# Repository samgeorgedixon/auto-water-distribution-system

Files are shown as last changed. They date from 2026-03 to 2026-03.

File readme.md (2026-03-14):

# Regulated Irrigation System (RIS)

**Modular, reliable and fine controlled irrigation for home to industrial greenhouses or farms, while adapting to varied temperatures and seasons to conserve water and ensure plant health.**

## Overview

Regulated Irrigation System (RIS) is modular irrigation system designed for everything from a small greenhouse to industrial farm setups. It gives you detailed control over watering routines and is able to adapt its watering output based on temperature and season. It does this while running reliably all year round unattended while conserving water.

From a phone / desktop browser you can schedule routines to water certain sets of plants at different times or intervals for durations based of current environment conditions.

#### Key Features

1. Water Plants (Water Conservation).
2. Any Environment and Scale (Greenhouse / Farm).
3. Reliable (Works for Months / Years).
4. Sustainable (Self Sufficient: Solar / Rain).
5. Relatively Affordable (< ~£100).

#### Modules

This design is made up of multiple modules which allow it to scale to any scenario with them able to sit flat on a table or be easily mounted onto a wall with keyholes.

- Command Module: Central, controlling all other modules based on the routines you have set.
- Switch modules: Add as many as needed where they interface with command to turn on certain ones of its 6 ports to power your water pumps or valves when needed.
- Valves / Pumps: Allow water to be pumped to specific sets of plants for different durations giving you full control.

#### Power

All operates off 1 battery that is charged continuously with a solar panel to ensure it can run for years in remote locations like an allotment or field.

You can then choose to power the pumps and valves by another source like mains or an external battery pack if they require more power in industrial environments.

## Small Greenhouse Scenario

To take advantage of it in this scenario you can have both sides of the greenhouse on different valves because they may get a different amount of sunlight or have different varieties of plant so one side needs more water than the other.

1. Then you can have a pump that is operated with each valve at a time taking water out of a water tank and distributing it but also have another that fills the tank every couple weeks with more water from a water butt.
2. Due to only giving the plants the water they need they will have increased yields, and it will conserve water which is important when using a water butt as when there is little rainfall it will still have leftover water.
3. As well as this due to water duration being done based of temperature, across the year plants will get more water in the summer when they need it more and little to none in the winter when they don’t need it.

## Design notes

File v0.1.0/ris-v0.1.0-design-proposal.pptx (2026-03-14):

## Regulated Irrigation System (RIS)

by Sam Dixon

What is it?

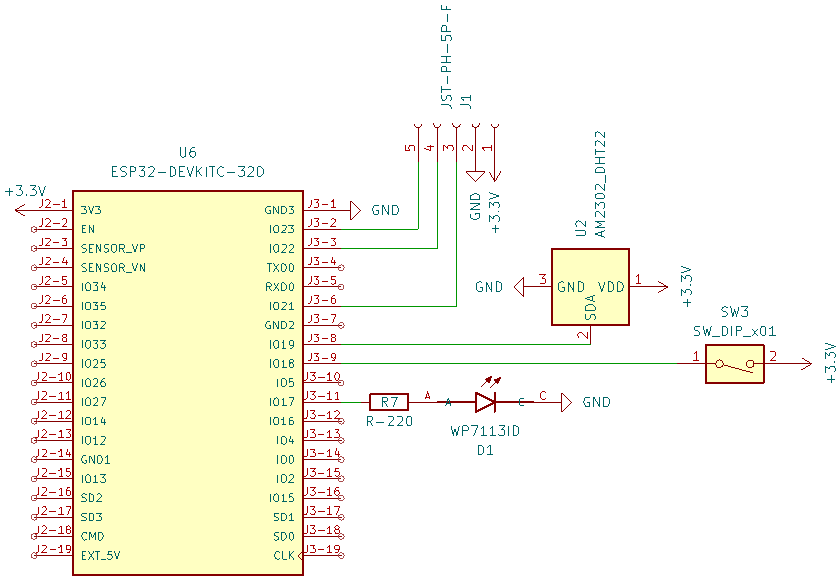
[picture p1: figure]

Command Module
Circuit

Circuit - Electronic Engineering

- This project is all about watering plants in any scenario possible like in a small greenhouse or across an entire farm while being reliable, able to continue working across a whole year through all the seasons.
- The idea for this project came from my Dad’s greenhouse which when we went on holiday was a struggle as no one could water the plants inside it.
- There are many existing products for this issue already, but they are either too expensive for no reason due to being sold to businesses or are too simple and not reliable enough, so I thought I’ll make my own.
- This all led me to my Design Brief I created:
  - Water Plants (Water Conservation).
  - Any Environment and Scale (Greenhouse / Farm).
  - Reliable (Works for Months / Years).
  - Sustainable (Self Sufficient: Solar / Rain).
  - Relatively Affordable (< ~£100).
- A significant portion of this project has been research based as I have been ensuring it can fit my strict design brief with the main consideration being “Any Environment and Scale” because it increases the possible use cases to fit as many users needs as possible.
- I am still currently developing this project and iterating over each area of the design outlined here (titles) over time getting closer to the final design that I will then produce and test as a prototype finally then producing it again as a final product (one-off for now).

Model - Mechanical Engineering

- There will be a circuit in the command and switch modules which I will organise onto 2 custom PCBs that I will get produced by JLCPCB as it is very cheap and scalable for batch production which I may consider if made into a product.
- Command Module which controls the entire system regulating all the valves and pumps at certain times contains: the microcontroller (ESP32), a temperature sensor, Wi-Fi switch, status LED and power management (battery, solar).
- Switch Module has multiple ports to turn on the valves and pumps bridging the gap between them and the command module containing: a shift register (74HC595) that will control relays (SRD-03VDC-SL-C) for each port.
- Each module will communicate using connectors (JST-PH) for power or data.

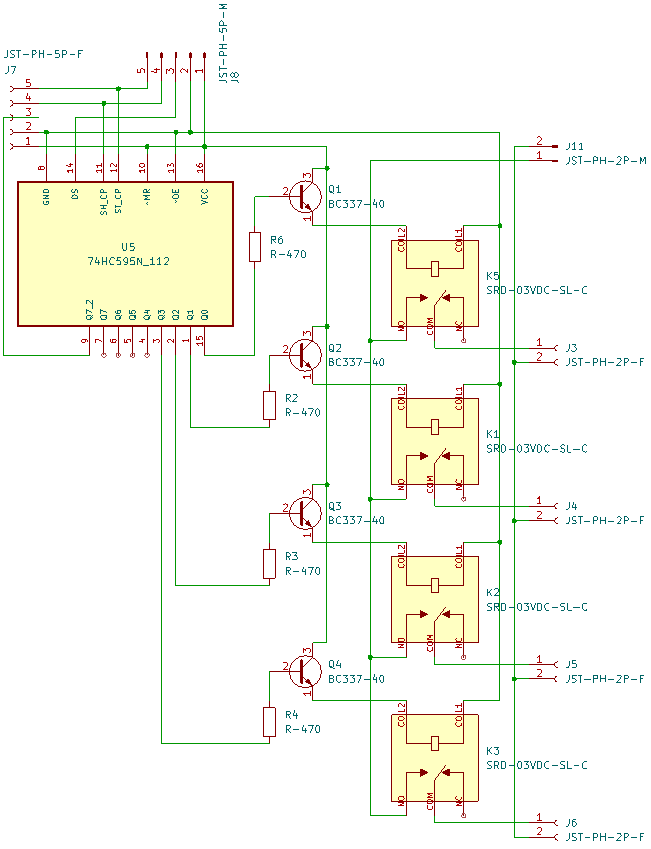
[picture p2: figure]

Switch Module
Circuit

Temp Sensor

Status LED

Wi-Fi Switch

ESP32 (MC)

Command Module

Shift Register

Shift Register

Relay

Relay

…

Valve

Pump

Regulation - Software Engineering

- The microcontroller (ESP32) will control the entire system, regulating all the valves and pumps to ensure they turn on at the required times, with the program (C++ Code) running on it.
- It creates a Wi-Fi Access Point Network with a Web Server as well that users can connect to even in the most remote locations to configure everything using the website interface (on a phone / laptop).
- Routines can then be created that will turn on certain switch ports (Pumps / Valves) at certain times (12:00 every day or month) for a certain duration (60s) to give full control allowing it to be used in any environment.
- This duration can change depending on the temperature sensor, for instance, if its hot (summer) then give plants more water (120s) or if its cold (winter) then give plants little to no water (0s) to allow it to function reliably all year-round while also being sustainable as it is only using the water it needs.
- This ability to use only the water it needs to will allow it to conserve water used in times of shortage and still be able to function through hosepipe bans for instance that have happened recently in the UK.
- All this customisation is given through the simple website that anyone can use to alter the functionality for their personal needs.
- I believe this control for the user is very important as it really sets it apart from the alternatives which really lack any of this leading to the user being unsatisfied with their product which this solves.

…

Switch Module

…

External

- This design is built up of multiple modules to allow it to be scaled up from just a couple plants to hundreds with each being a 3D printed (due to it being more cost effective) case that slide into each other on the sides.
- The Command Module will be the same across all implementations of the product containing the microcontroller (ESP32) for the regulation and a battery with a solar panel on top.
- The Valve Modules contain many slots for electromechanical valves (Solenoid) that can send off water to different areas or types of plants that may want different amount of water.
- The Pumps are external parts of the design that may have module enclosers in the future to protect them while they pump the water to the valves and then plants when needed.
- The Switch Modules control relays for ports to the valves or pumps when needed and can be chained together due to the shift registers inside to allow as many valves and pumps as possible to be added for the required scale.
- An example of an application of this project would be in a greenhouse where the plants on one side need to get more water (due to sunlight) that the other so could be on a different valve port meaning one side has it open for longer than the other allowing full control for the user over their plants or crops (same principle could be applied to a farm).

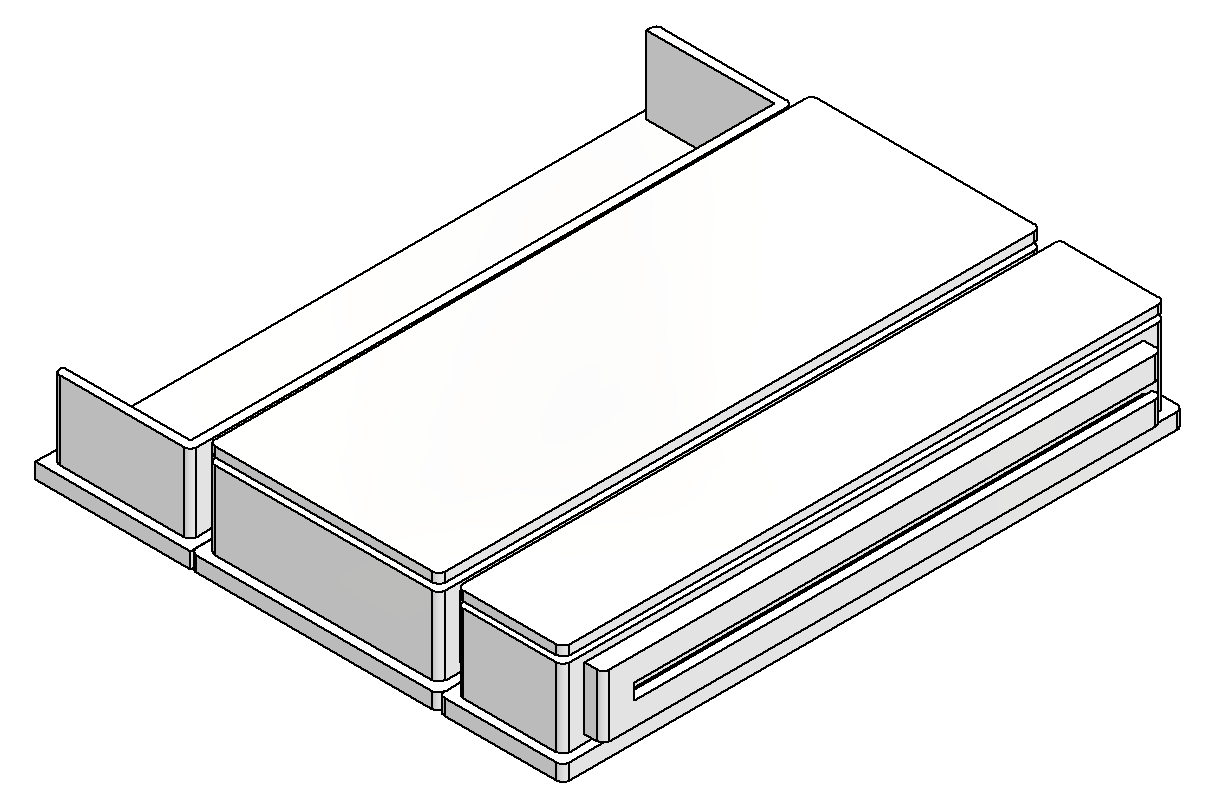
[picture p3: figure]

Valve Module

Command Module

Switch Module

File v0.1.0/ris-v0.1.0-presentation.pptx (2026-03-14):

## Regulated Irrigation System (RIS)

by Sam Dixon

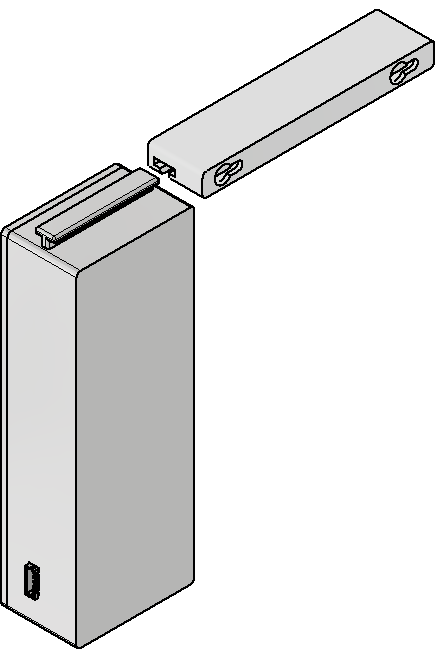
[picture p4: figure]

What is it?

Key Points

- Water Plants (Water Conservation).
- Any Environment and Scale (Greenhouse / Farm).
- Reliable (Works for Months / Years).
- Sustainable (Self Sufficient: Solar / Rain).
- Relatively Affordable (< ~£100).

Wall Mount

- This is an irrigation system all about watering plants in any scenario possible like in a small greenhouse or industrial greenhouse due to giving you full control over its operation while being reliable, able to continue working across a whole year through all the seasons.
- For instance, using the website interface on your phone you can set routines to water certain sets of plants at certain times for a duration based of the current temperature.
- This allows all different types of plants to get the correct amount of water with no wasted.

Power

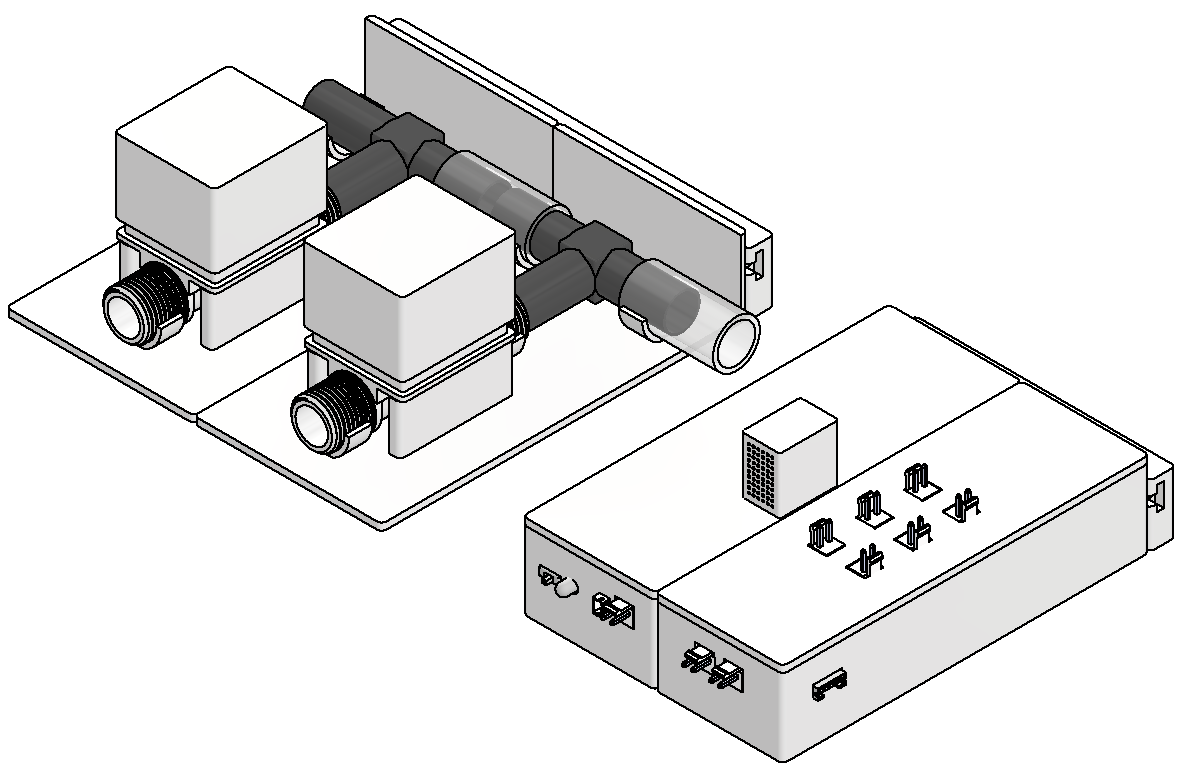
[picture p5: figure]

- It all operates off 1 battery that is charged continuously with a solar panel to ensure it can run for years in remote locations like an allotment or field.
- You can choose to power the pumps and valves by another source like mains or an external battery pack if they require more power in industrial environments.

Modules

- This design is made up of multiple modules which allow it to scale to any scenario with them able to sit flat on a table or be easily mounted onto a wall with keyholes.
- The command module is central, controlling all other modules based on the routines you have set.
- Each valve is chained together on a module to allow water to be pumped to specific sets of plants for different durations giving you control.
- You can add as many switch modules as needed where they interface with command to turn on certain ones of its 6 ports to power the water pumps or valves when needed.

Valve 1

Valve 2

Valve Module

Valve Module

Command
Module

Switch
Module

Ports

## Regulated Irrigation System (RIS)

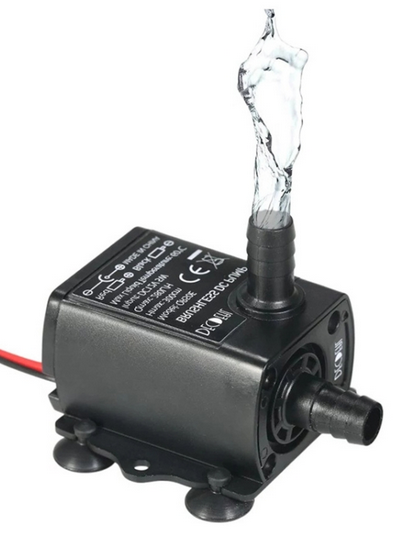
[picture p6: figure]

Pump - 1

by Sam Dixon

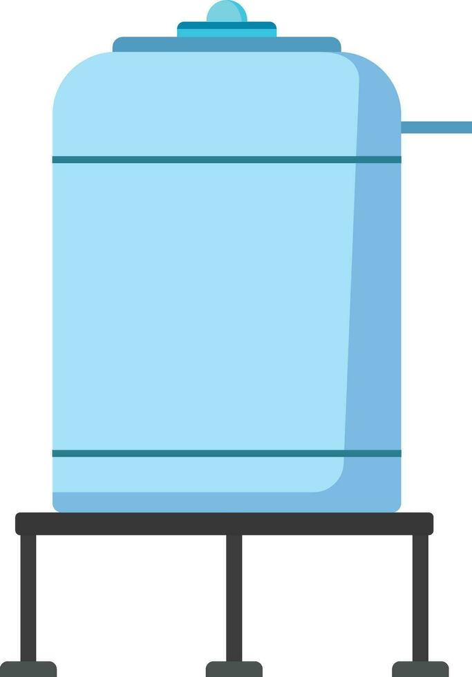
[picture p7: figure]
Water tank flat style vector illustration, Water storage tank, container for storing water, cistern stock vector image 33123783 Vector Art at Vecteezy

Water Tank

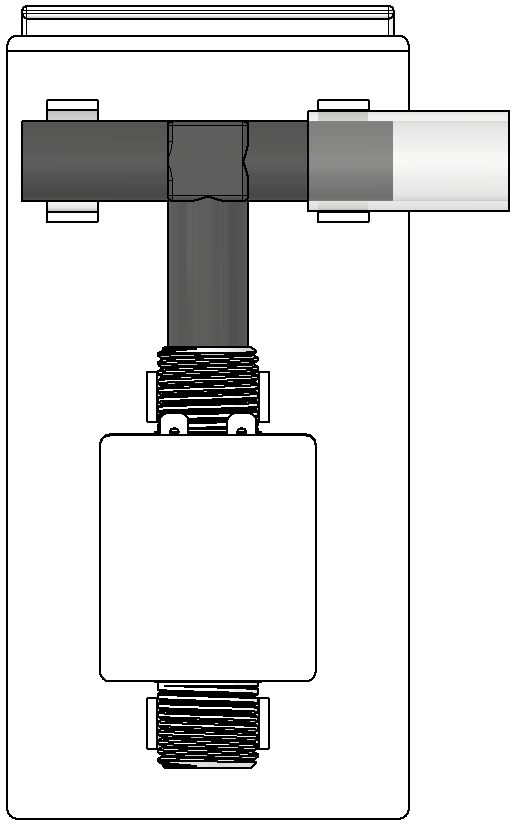
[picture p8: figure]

Valve
Module
1

Valve
Module
2

… Valve Modules

Pump 2

Pump - 2

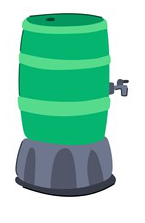
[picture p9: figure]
378 Water Butt Stock Vectors and Vector Art | Shutterstock

Water Butt

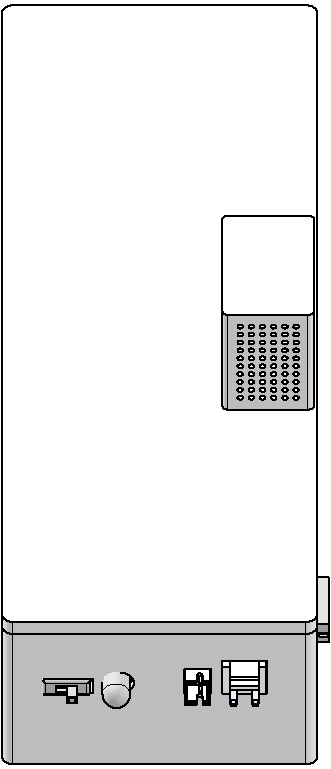
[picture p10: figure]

Command
Module

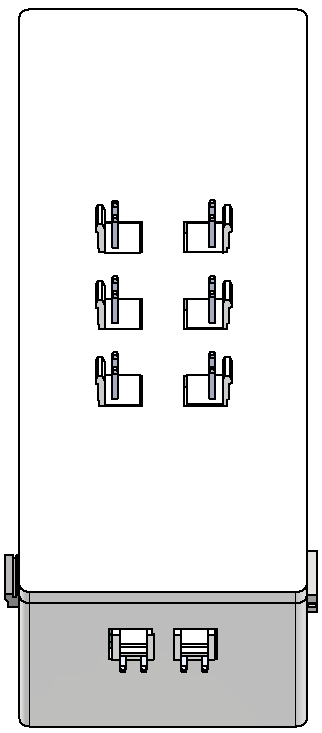
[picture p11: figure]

Switch
Module - 1

Switch
Module - 2

Small Greenhouse Scenario

- To take advantage of it in this scenario you can have both sides of the greenhouse on different valves because they may get a different amount of sunlight or have different varieties of plant so one side needs more water than the other.
- Then you can have a pump that is operated with each valve at a time taking water out of a water tank and distributing it but also have another that fills the tank every couple weeks with more water from a water butt.
- Due to only giving the plants the water they need they will have increased yields, and it will conserve water which is important when using a water butt as when there is little rainfall it will still have leftover water.
- As well as this due to water duration being done based of temperature, across the year plants will get more water in the summer when they need it more and little to none in the winter when they don’t need it.

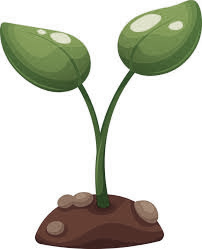
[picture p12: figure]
Sprout of plant, small plant with piece of earth in cartoon style
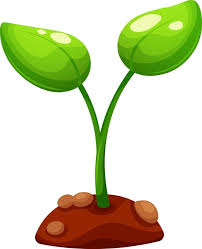
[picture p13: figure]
Sprout of plant, small plant with piece of earth in cartoon style

… Switch Modules

Solar Charging

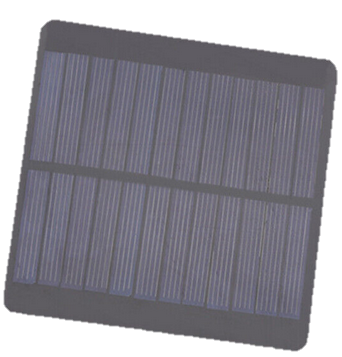
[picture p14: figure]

Solar Panel

Power Chaining …

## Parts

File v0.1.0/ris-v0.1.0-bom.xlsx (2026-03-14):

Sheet: bom
BOM
Component |  |  |  |  | Order
Store | Name | Part Number | Info | Min Quantity | Unit Price | Shipping | PC's | Needed to Buy | Total Price | Shipping Time (Days) | Link
JLCPCB |  |  | PCB's |  |  | £1.12 |  | 1 | £1.12 | 10 - 14 | JLCPCB (https://cart.jlcpcb.com/shopcart/cart?_t=1767553829179&up_spm=Jlcpcb.Loginpage.1003)
- | Command Module | v1.0.0 |  | 1 | £0.86 | £0.00 | 5 | 1 | £0.86 | -
- | Switch Module | v1.0.0 |  | 1 | £0.86 | £0.00 | 5 | 1 | £0.86 | -
LCSC |  |  |  |  | £2.20 | £5.94 |  | 1 | £8.14 | 7 - 15 | LCSC (https://www.lcsc.com/cart)
- | JST-VH Male 2pin | B2P-VH(LF)(SN) |  | 3 | £0.41 | £0.00 | 10 | 1 | £0.41 | - | LCSC (https://www.lcsc.com/product-detail/C160315.html)
- | Switch | SS-12D00-G3 | 2state | 1 | £0.16 | £0.00 | 3 | 1 | £0.16 | - | LCSC (https://www.lcsc.com/product-detail/C22355741.html)
- | JST-PH Male 5pin | B5B-PH-K-S(LF)(SN) |  | 3 | £0.38 | £0.00 | 10 | 1 | £0.38 | - | LCSC (https://www.lcsc.com/product-detail/C157993.html)
- | Mosfet | IRLZ44N(UMW) | 3.3V: 5A-12V | 6 | £3.22 | £0.00 | 15 | 1 | £3.22 | - | LCSC (https://www.lcsc.com/product-detail/C42370423.html)
- | Diode | SB560_AY_10001 | 5A | 6 | £1.34 | £0.00 | 15 | 1 | £1.34 | - | LCSC (https://www.lcsc.com/product-detail/C282379.html)
- | Shift Register | 74HC595N | 8bit | 1 | £0.52 | £0.00 | 5 | 1 | £0.52 | - | LCSC (https://www.lcsc.com/product-detail/C507175.html)
- | JST-PH Male 2pin | B2B-PH-K-S(LF)(SN) |  | 1 | £0.43 | £0.00 | 20 | 1 | £0.43 | - | LCSC (https://www.lcsc.com/product-detail/C131337.html)
- | Header 3pin | PM2.54-1X3P-H85 |  | 1 | £0.11 | £0.00 | 5 | 1 | £0.11 | - | LCSC (https://www.lcsc.com/product-detail/C42431866.html)
 | Header 19pin | PM2.54-1*19 |  | 2 | £0.69 | £0.00 | 5 | 1 | £0.69 | - | LCSC (https://www.lcsc.com/product-detail/C5371990.html?s_z=n_PM2.54-1X19P-H85)
AliExpress |  |  |  |  |  |  |  | 1 | £0.00 | 8 - 12 | AliExpress (https://www.aliexpress.com/p/shoppingcart/index.html?spm=a2g0o.cart.header.1.97d438da5Uqi5N)
- | Temp Sensor | DHT22 |  | 1 | £1.79 | £0.00 | 1 | 1 | £1.79 | - | AliExpress (https://www.aliexpress.com/item/1005010342821748.html?mp=1)
- | Pipe: Flexible PVC |  | 1m: ID-12mm | 1 | £3.09 | £0.00 | 1 | 1 | £3.09 | - | AliExpress (https://www.aliexpress.com/item/1005008851917137.html?mp=1)
- | Pipe Reducer |  | 3.9mm - 12.7mm | 2 | £0.76 | £0.00 | 5 | 1 | £0.76 | - | AliExpress (https://www.aliexpress.com/item/1005005912274158.html?mp=1)
- | Boost Converter | MT3608 | 2A OUT | 2 | £1.89 | £0.00 | 5 | 1 | £1.89 | - | AliExpress (https://www.aliexpress.com/item/1005008953348410.html?mp=1)
- | Wire: JST-VH 2pin |  | 10cm: Double Ended | 2 | £1.27 | £0.00 | 5 | 1 | £1.27 | - | AliExpress (https://www.aliexpress.com/item/1005009025003911.html?mp=1)
- | Wire: JST-PH 2pin |  | 20cm: Single Ended | 1 | £0.90 | £0.00 | 10 | 1 | £0.90 | - | AliExpress (https://www.aliexpress.com/item/1005007270514533.html?mp=1)
- | Wire: JST-PH 5pin |  | 20cm: Single Ended | 2 | £1.82 | £0.00 | 10 | 1 | £1.82 | - | AliExpress (https://www.aliexpress.com/item/1005007270514533.html?mp=1)
- | Pipe Reducer |  | 11.1mm - 15.8mm | 3 | £2.01 | £0.00 | 5 | 1 | £2.01 | - | AliExpress (https://www.aliexpress.com/item/1005005912274158.html?mp=1)
- | Pump | QR50E | 5W: 12V (3m Lift, 280l/h) | 1 | £3.83 | £0.00 | 1 | 1 | £3.83 | - | AliExpress (https://www.aliexpress.com/item/1005007457199939.html?mp=1)
- | Solenoid Valve | FPD-270A | 12V: G1/2" NC | 2 | £3.08 | £0.00 | 1 | 2 | £6.16 | - | AliExpress (https://www.aliexpress.com/item/1005007532380394.html?mp=1)
- | RTC Module | ZS-042 |  | 1 | £1.94 | £0.00 | 1 | 1 | £1.94 | - | AliExpress (https://www.aliexpress.com/item/32985147642.html?mp=1)
- | Battery | 5050100 | 4Ah: 3.7V | 1 | £5.99 | £2.81 | 1 | 1 | £8.80 | 18 | AliExpress (https://www.aliexpress.com/item/32908593252.html?mp=1)
Ebay |  |  |  |  |  |  |  | 1 | £0.00 |  | Ebay (https://cart.ebay.co.uk/)
- | ESP32 | ESP32-DevKitC-v4 |  | 1 | £5.95 | £0.00 | 1 | 1 | £5.95 | 3 - 4 | Ebay (https://www.ebay.co.uk/itm/195759492546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)
- | Battery Charger |  | 1A: 5V IN, 4.2V OUT | 1 | £2.88 | £1.66 | 1 | 1 | £4.54 | 8 - 10 | Ebay (https://www.ebay.co.uk/itm/254771123006?_skw=Li-ion+charge+controller&itmmeta=01KCE8GVJEVT9J6W3MWF6TEBNC)
- | Solar Cell |  | 150mA: 5V | 1 | £2.74 | £0.00 | 1 | 1 | £2.74 | 12 - 16 | Ebay (https://www.ebay.co.uk/itm/335504833393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)
- | Pipe: Flexible PVC |  | 2m: ID-16mm (1/2") | 1 | £3.80 | £0.00 | 1 | 1 | £3.80 | 2 - 3 | Ebay (https://www.ebay.co.uk/itm/333369363332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)
- | T-Piece |  | 1/2" (OD-16mm) | 2 | £3.99 | £0.00 | 2 | 1 | £3.99 | 2 - 3 | Ebay (https://www.ebay.co.uk/itm/133052308194?_skw=T-Piece&itmmeta=01KF5W1XYFVM32WJARDY9XMV77&var=432352315321)
3D Print | Casing (Model) |  | 3D Printed | 1 | £0.00 | £0.00 |  | 1 | £0.00 | 0
Total |  |  |  |  |  |  |  |  | £73.52

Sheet: store-orders
BOM
Component |  |  | Order
Store Basket | Info | Min Quantity | Unit Price | Shipping | Needed to Buy | Total Price | Shipping Time (Days) | Link
JLCPCB | PCB's | 2 | £1.72 | £1.12 | 1 | £2.84 | 10 - 14 | JLCPCB (https://cart.jlcpcb.com/shopcart/cart?_t=1767553829179&up_spm=Jlcpcb.Loginpage.1003)
LCSC | Electronics | 8 | £9.53 | £5.94 | 1 | £15.47 | 7 - 15 | LCSC (https://www.lcsc.com/cart)
AliExpress | Components | 12 | £31.45 | £2.81 | 1 | £34.26 | 8 - 12, 18 | AliExpress (https://www.aliexpress.com/p/shoppingcart/index.html?spm=a2g0o.cart.header.1.97d438da5Uqi5N)
Ebay | Components | 5 | £19.50 | £1.66 | 1 | £21.16 | 9 - 10 | Ebay (https://cart.ebay.co.uk/)
Casing (Model) | 3D Printed | 2 | £0.00 | £0.00 | 1 | £0.00 | 0
Total |  |  |  |  |  | £73.73

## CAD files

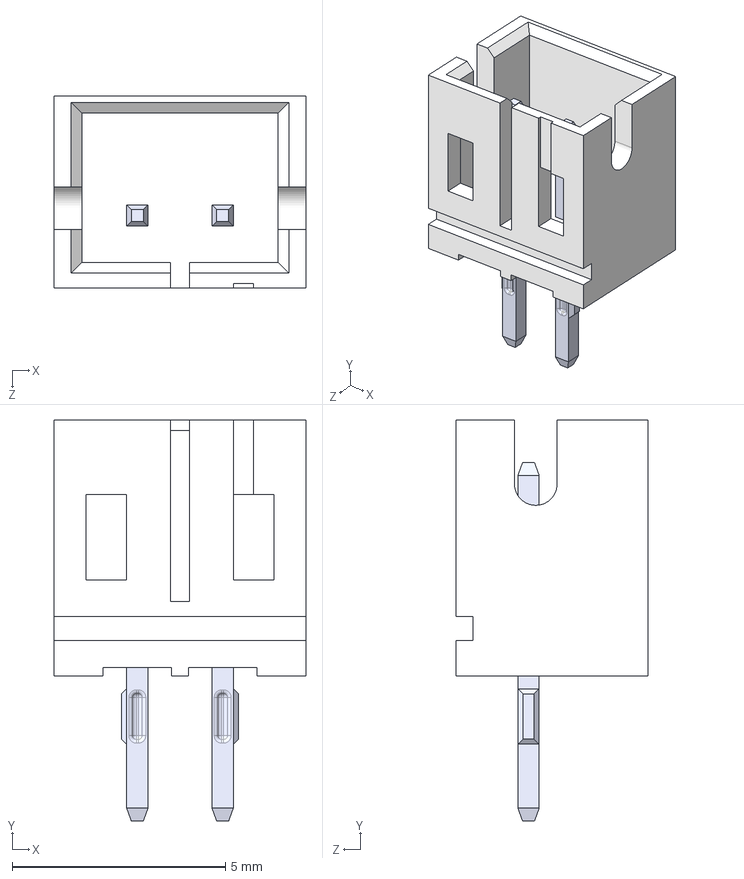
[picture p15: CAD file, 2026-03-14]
model/asm/electronic-components/jst-ph-2p/B2B-PH-K-S--3DModel-STEP-56544.STEP
5.90 x 9.40 x 4.50 mm

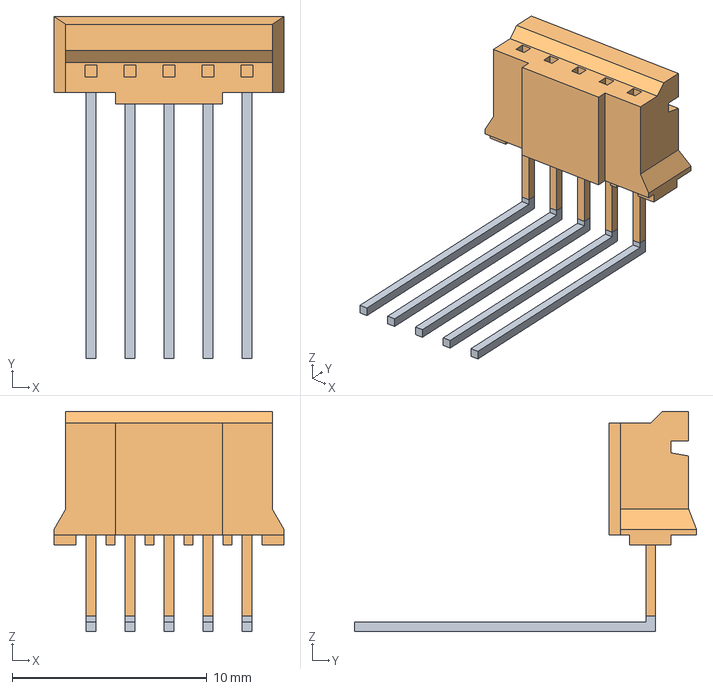
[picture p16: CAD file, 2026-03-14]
model/asm/electronic-components/jst-ph-5p/jst-ph-r5.step
11.8 x 17.5 x 11.3 mm
jst-ph-5p_wire x 5
PHR-5

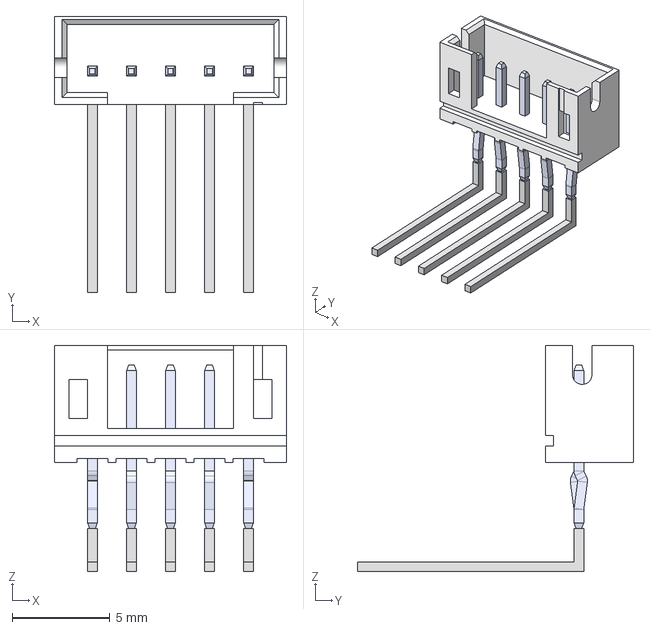
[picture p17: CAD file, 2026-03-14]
model/asm/electronic-components/jst-ph-5p_short/jst-ph-5p_short.step
11.9 x 14.2 x 11.6 mm
B5B-PH-K-S(LF)(SN)
jst-ph-5p_wire x 5

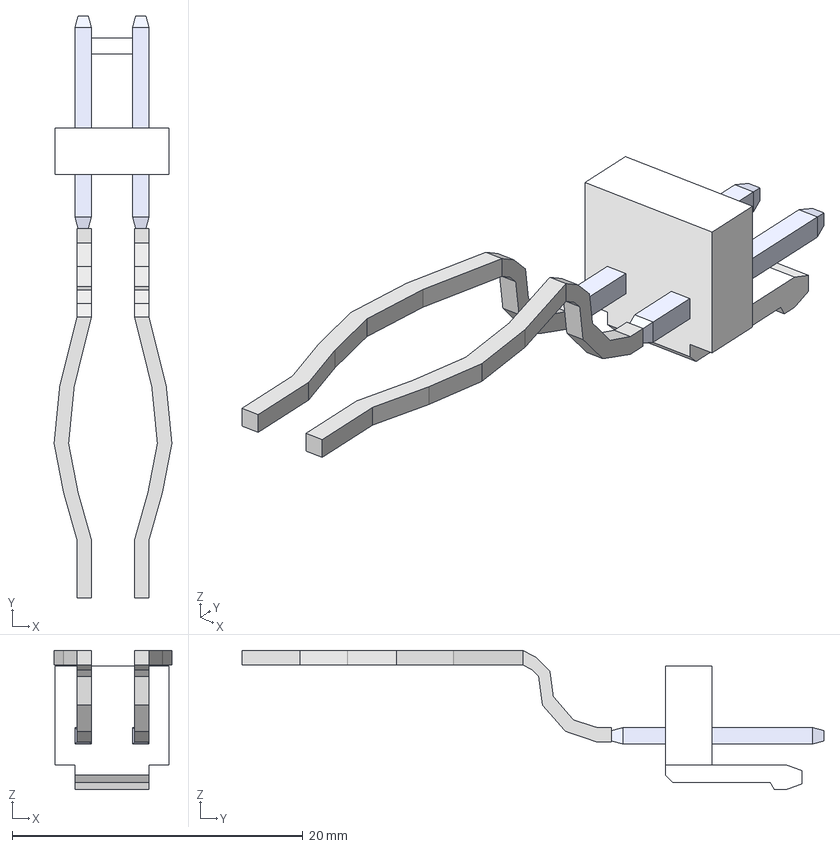
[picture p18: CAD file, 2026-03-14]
model/asm/electronic-components/jst-vh-2p/jst-vh-2p.step
8.10 x 40.0 x 9.57 mm
BxP-VH_2
pin x 2
jst-vh-2p_wire
jst-vh-2p_wire_MIR

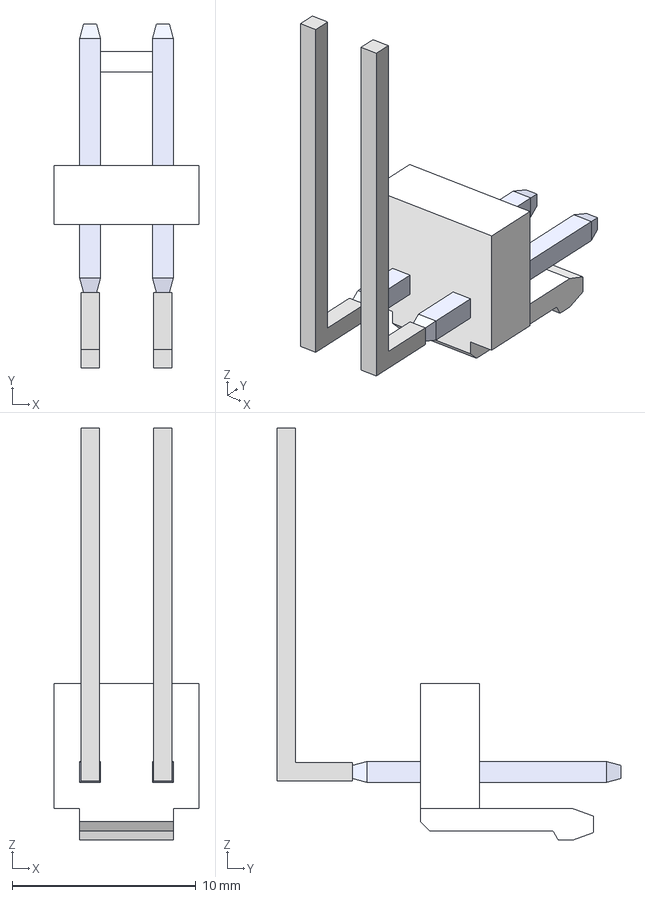
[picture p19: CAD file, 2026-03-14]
model/asm/electronic-components/jst-vh-2p_short/jst-vh-2p_short-up.step
7.86 x 18.7 x 22.4 mm
BxP-VH_2
pin x 2
jst-vh-2p_wire x 2

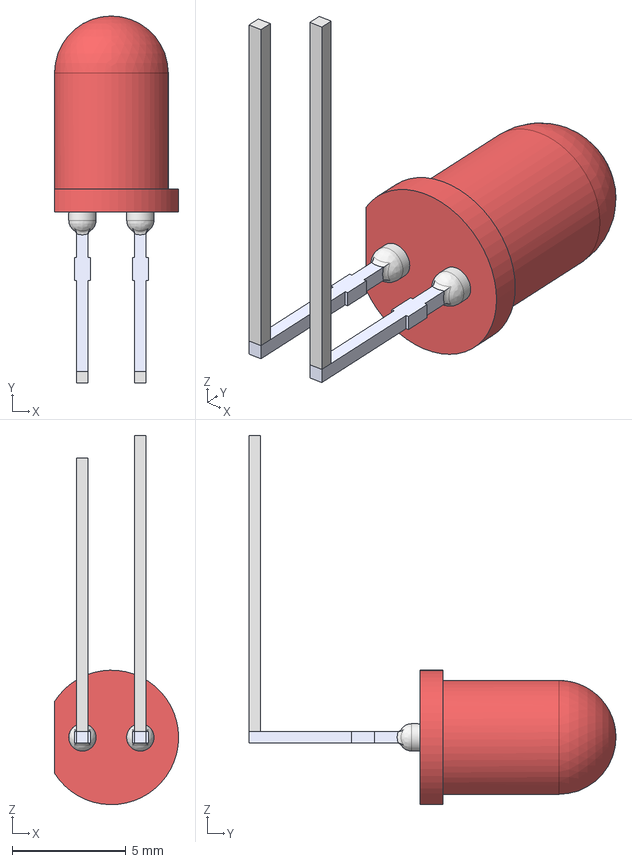
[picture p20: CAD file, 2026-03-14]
model/asm/electronic-components/led/led.step
5.45 x 16.1 x 16.2 mm
WP7113ID_WP7113ID
led-wire-long
led-wire-long_1

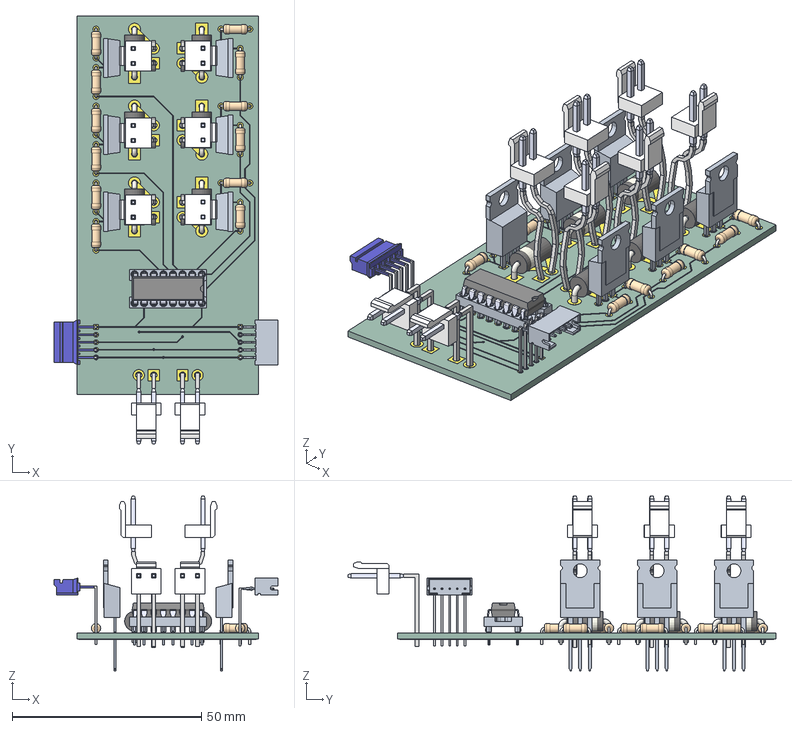
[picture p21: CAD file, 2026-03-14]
model/asm/electronic-components/ris_switch-module.step
59.1 x 113.1 x 46.2 mm
jst-vh-2p x 6
R_Axial_DIN0207_L63mm_D25mm_P762mm_Horizontal x 12
IRF9540N x 6
SOT38-4
D_DO-201AD_P12.70mm_Horizontal x 6
jst-vh-2p_short-up x 2
jst-ph-5p
jst-ph-r5
ris_switch-module_track_1
ris_switch-module_track_2
ris_switch-module_track_3
ris_switch-module_track_4
ris_switch-module_track_5
ris_switch-module_track_6
ris_switch-module_track_7
ris_switch-module_track_8
ris_switch-module_track_9
ris_switch-module_track_10
ris_switch-module_track_11
ris_switch-module_track_12
ris_switch-module_track_13
ris_switch-module_track_14
ris_switch-module_track_15
ris_switch-module_track_16
ris_switch-module_track_17
ris_switch-module_track_18
ris_switch-module_track_19
ris_switch-module_track_20
ris_switch-module_track_21
ris_switch-module_track_22
ris_switch-module_track_23
ris_switch-module_track_24
ris_switch-module_track_25
ris_switch-module_track_26
ris_switch-module_track_27
ris_switch-module_track_28
ris_switch-module_track_29
ris_switch-module_track_30
ris_switch-module_track_31
ris_switch-module_track_32
ris_switch-module_track_33
ris_switch-module_track_34
ris_switch-module_track_35
ris_switch-module_track_36
ris_switch-module_track_37
ris_switch-module_track_38
ris_switch-module_track_39
ris_switch-module_track_40
ris_switch-module_track_41
ris_switch-module_track_42
ris_switch-module_track_43
ris_switch-module_track_44
ris_switch-module_track_45
ris_switch-module_track_46
ris_switch-module_track_47
ris_switch-module_track_48
ris_switch-module_track_49
ris_switch-module_track_50
ris_switch-module_track_51
ris_switch-module_track_52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

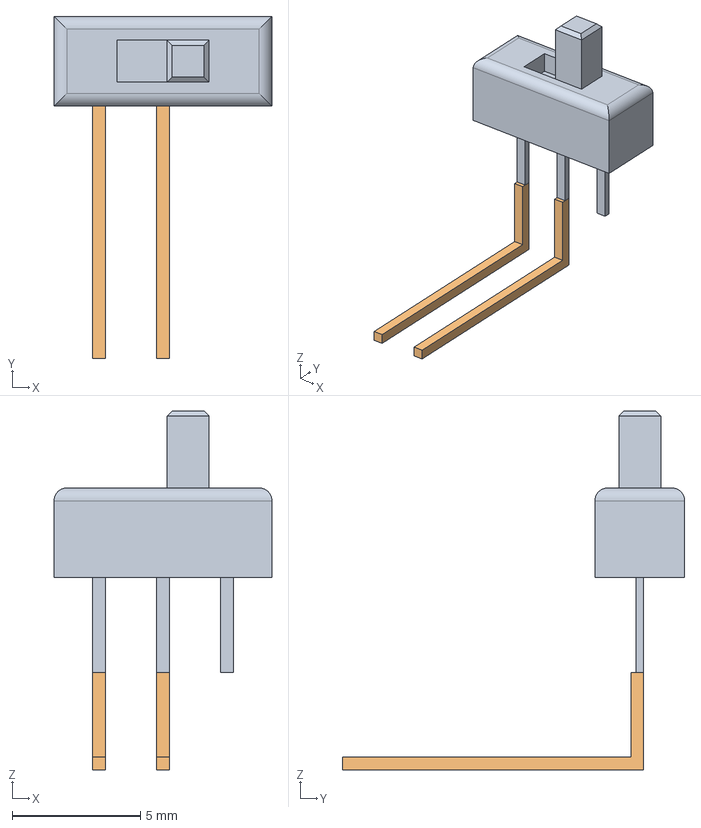
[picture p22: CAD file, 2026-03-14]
model/asm/electronic-components/switch/switch.step
8.50 x 13.4 x 14.0 mm
switch_1
switch-wire x 2

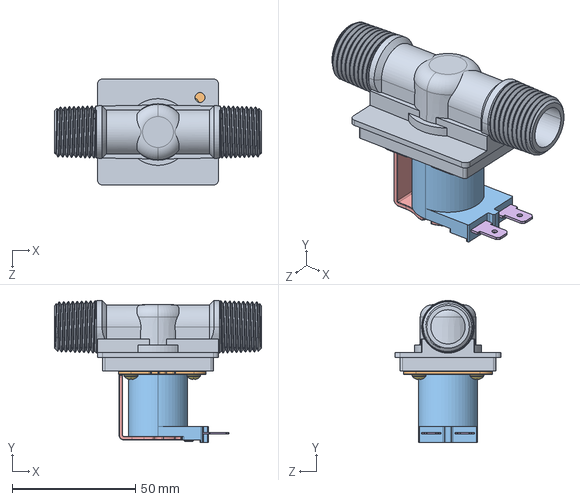
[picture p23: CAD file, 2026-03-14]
model/asm/electronic-components/valve-solenoid/solenoid-valve.STEP
83.8 x 57.5 x 42.9 mm

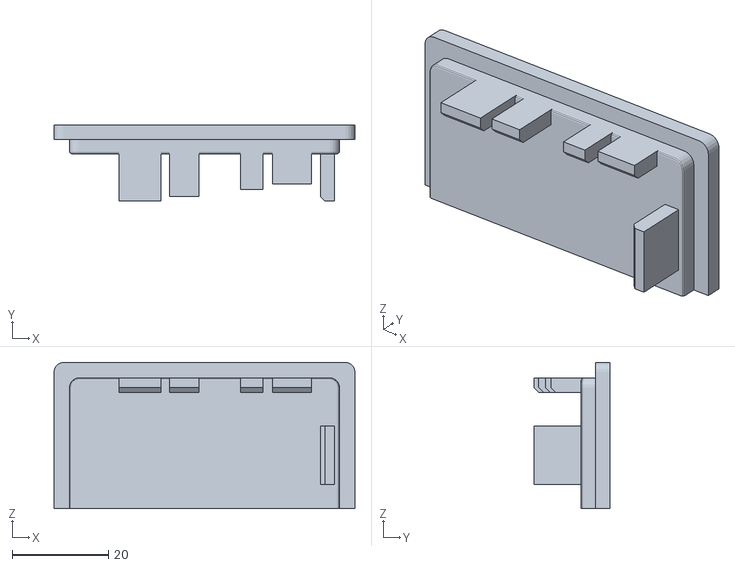
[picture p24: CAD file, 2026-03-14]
model/models/module-command/module-lid_command-port-jig.stl
62.4 x 15.8 x 30.3

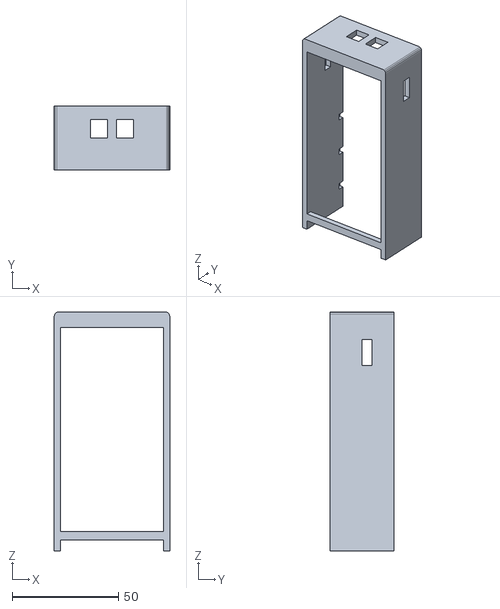
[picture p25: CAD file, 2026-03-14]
model/models/module-switch/module_switch-port-jig.stl
54.4 x 30.0 x 112.5

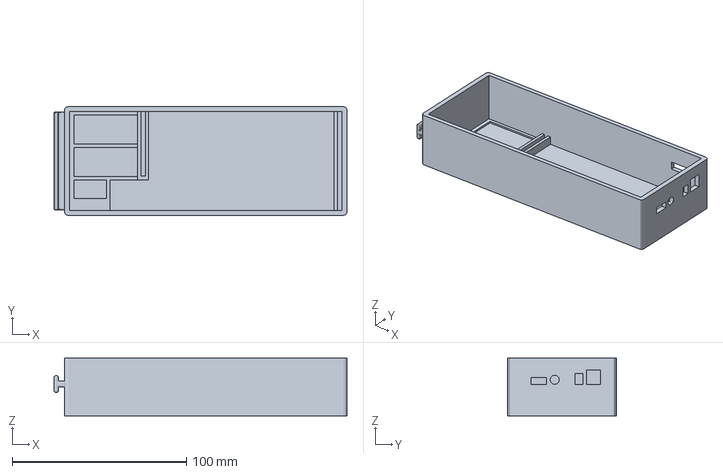
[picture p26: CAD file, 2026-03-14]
model/models/prints-v0.1.0/ris-print-5.3mf
168.0 x 62.4 x 33.0 mm

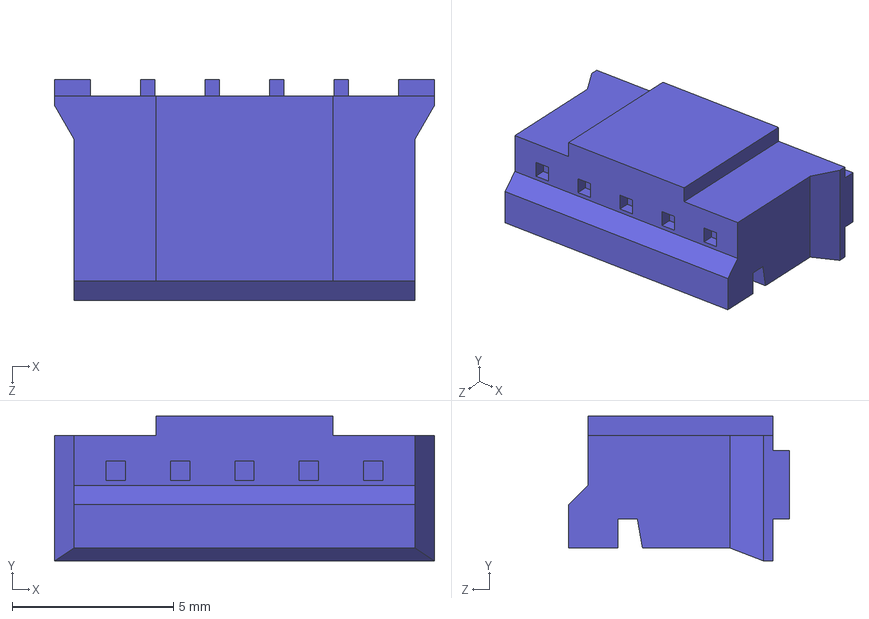
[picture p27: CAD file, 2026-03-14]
model/asm/electronic-components/jst-ph-5p/PHR-5.STEP
11.8 x 4.50 x 6.85 mm

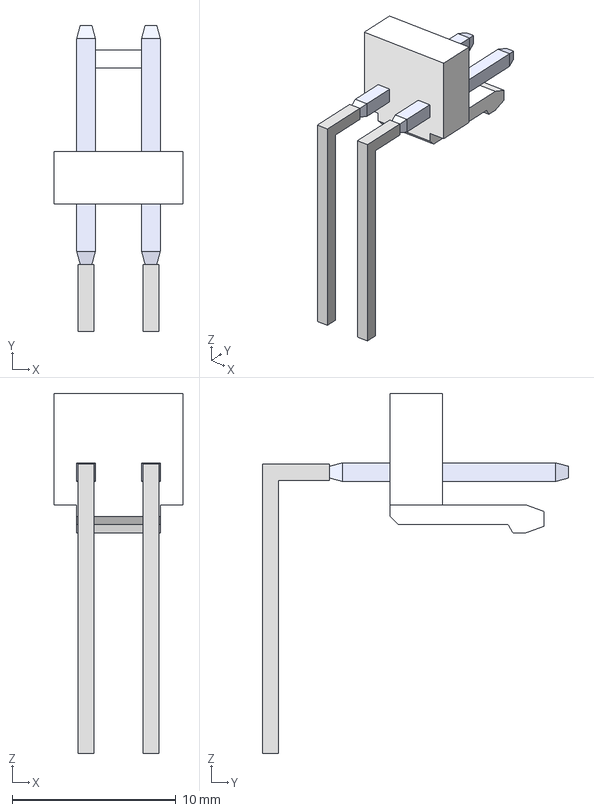
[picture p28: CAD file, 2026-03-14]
model/asm/electronic-components/jst-vh-2p_short/jst-vh-2p_short-down.step
7.86 x 18.7 x 22.0 mm
BxP-VH_2
pin x 2
jst-vh-2p_wire x 2

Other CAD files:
model/ris-design.dwg
model/asm/electronic-components/ris_command-module.step
model/asm/electronic-components/switch/final_slide_switch_3mm_spdt.step
model/models/module-command/sheet-battery-protection.stl
model/asm/electronic-components/AM2302_dht22.step
model/asm/electronic-components/battery-5050100_4000.ipt
model/asm/electronic-components/boost-converter.ipt
model/asm/electronic-components/charge-controller.ipt
model/asm/electronic-components/jst-ph-2p/jst-ph-2p.iam
model/asm/electronic-components/jst-ph-5p/jst-ph-5p.iam
model/asm/electronic-components/jst-ph-5p/jst-ph-5p.step
model/asm/electronic-components/jst-ph-5p/jst-ph-5p_wire.ipt
model/asm/electronic-components/jst-ph-5p/jst-ph-r5.iam
model/asm/electronic-components/jst-ph-5p/jst-ph-r5.ipt
model/asm/electronic-components/jst-ph-5p_short/jst-ph-5p_short.iam
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

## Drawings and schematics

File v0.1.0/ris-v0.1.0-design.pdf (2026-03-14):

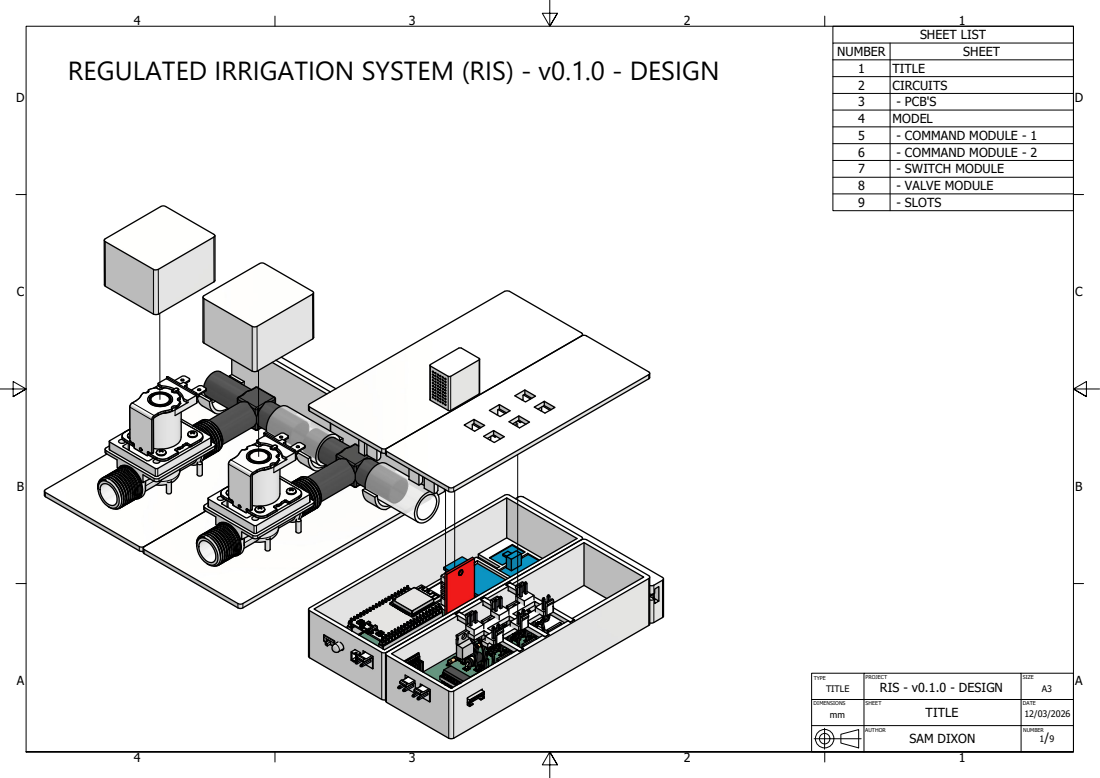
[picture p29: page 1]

SHEET LIST

NUMBER | SHEET
1 | TITLE
2 | CIRCUITS
3 | - PCB'S
4 | MODEL
5 | - COMMAND MODULE - 1
6 | - COMMAND MODULE - 2
7 | - SWITCH MODULE
8 | - VALVE MODULE
9 | - SLOTS

REGULATED IRRIGATION SYSTEM (RIS) - v0.1.0 - DESIGN

TYPE TITLE | PROJECT RIS - v0.1.0 - DESIGN | SIZE A3

DIMENSIONS mm | SHEET TITLE | DATE

AUTHOR SAM DIXON | NUMBER

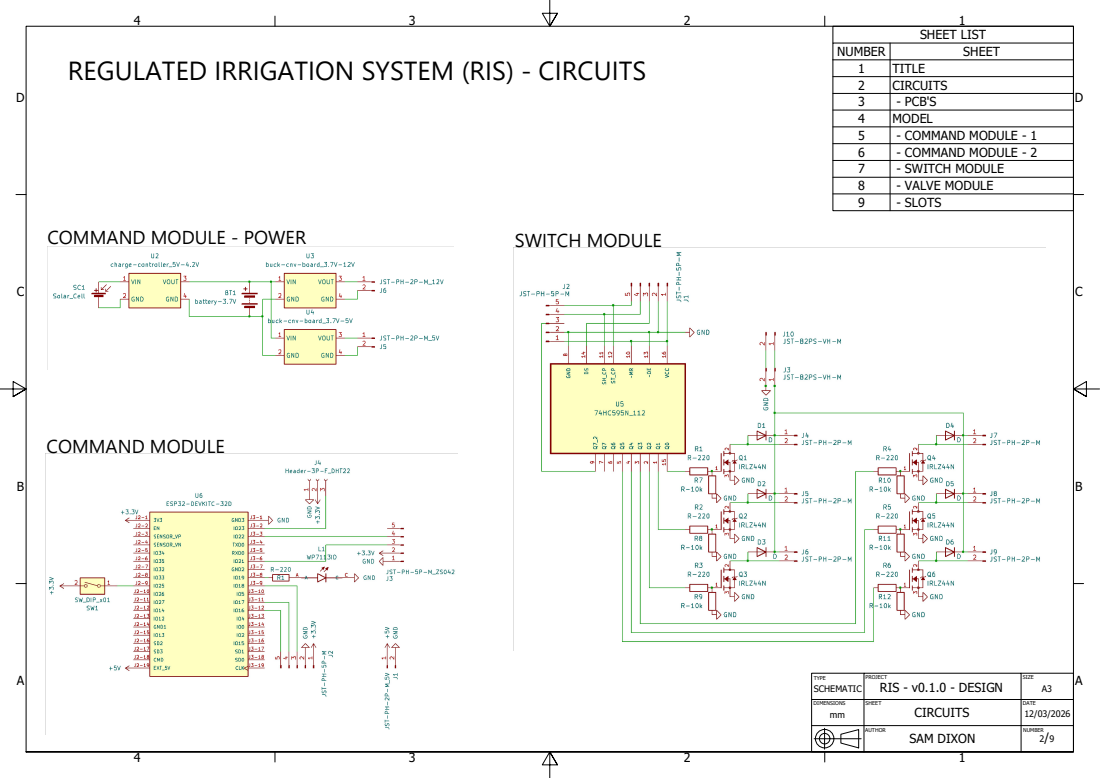
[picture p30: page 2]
COMMAND MODULE; SWITCH MODULE

SHEET LIST

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

REGULATED IRRIGATION SYSTEM (RIS) - CIRCUITS

COMMAND MODULE - POWER

TYPE SCHEMATIC | PROJECT RIS - v0.1.0 - DESIGN | SIZE A3

DIMENSIONS | SHEET CIRCUITS | DATE

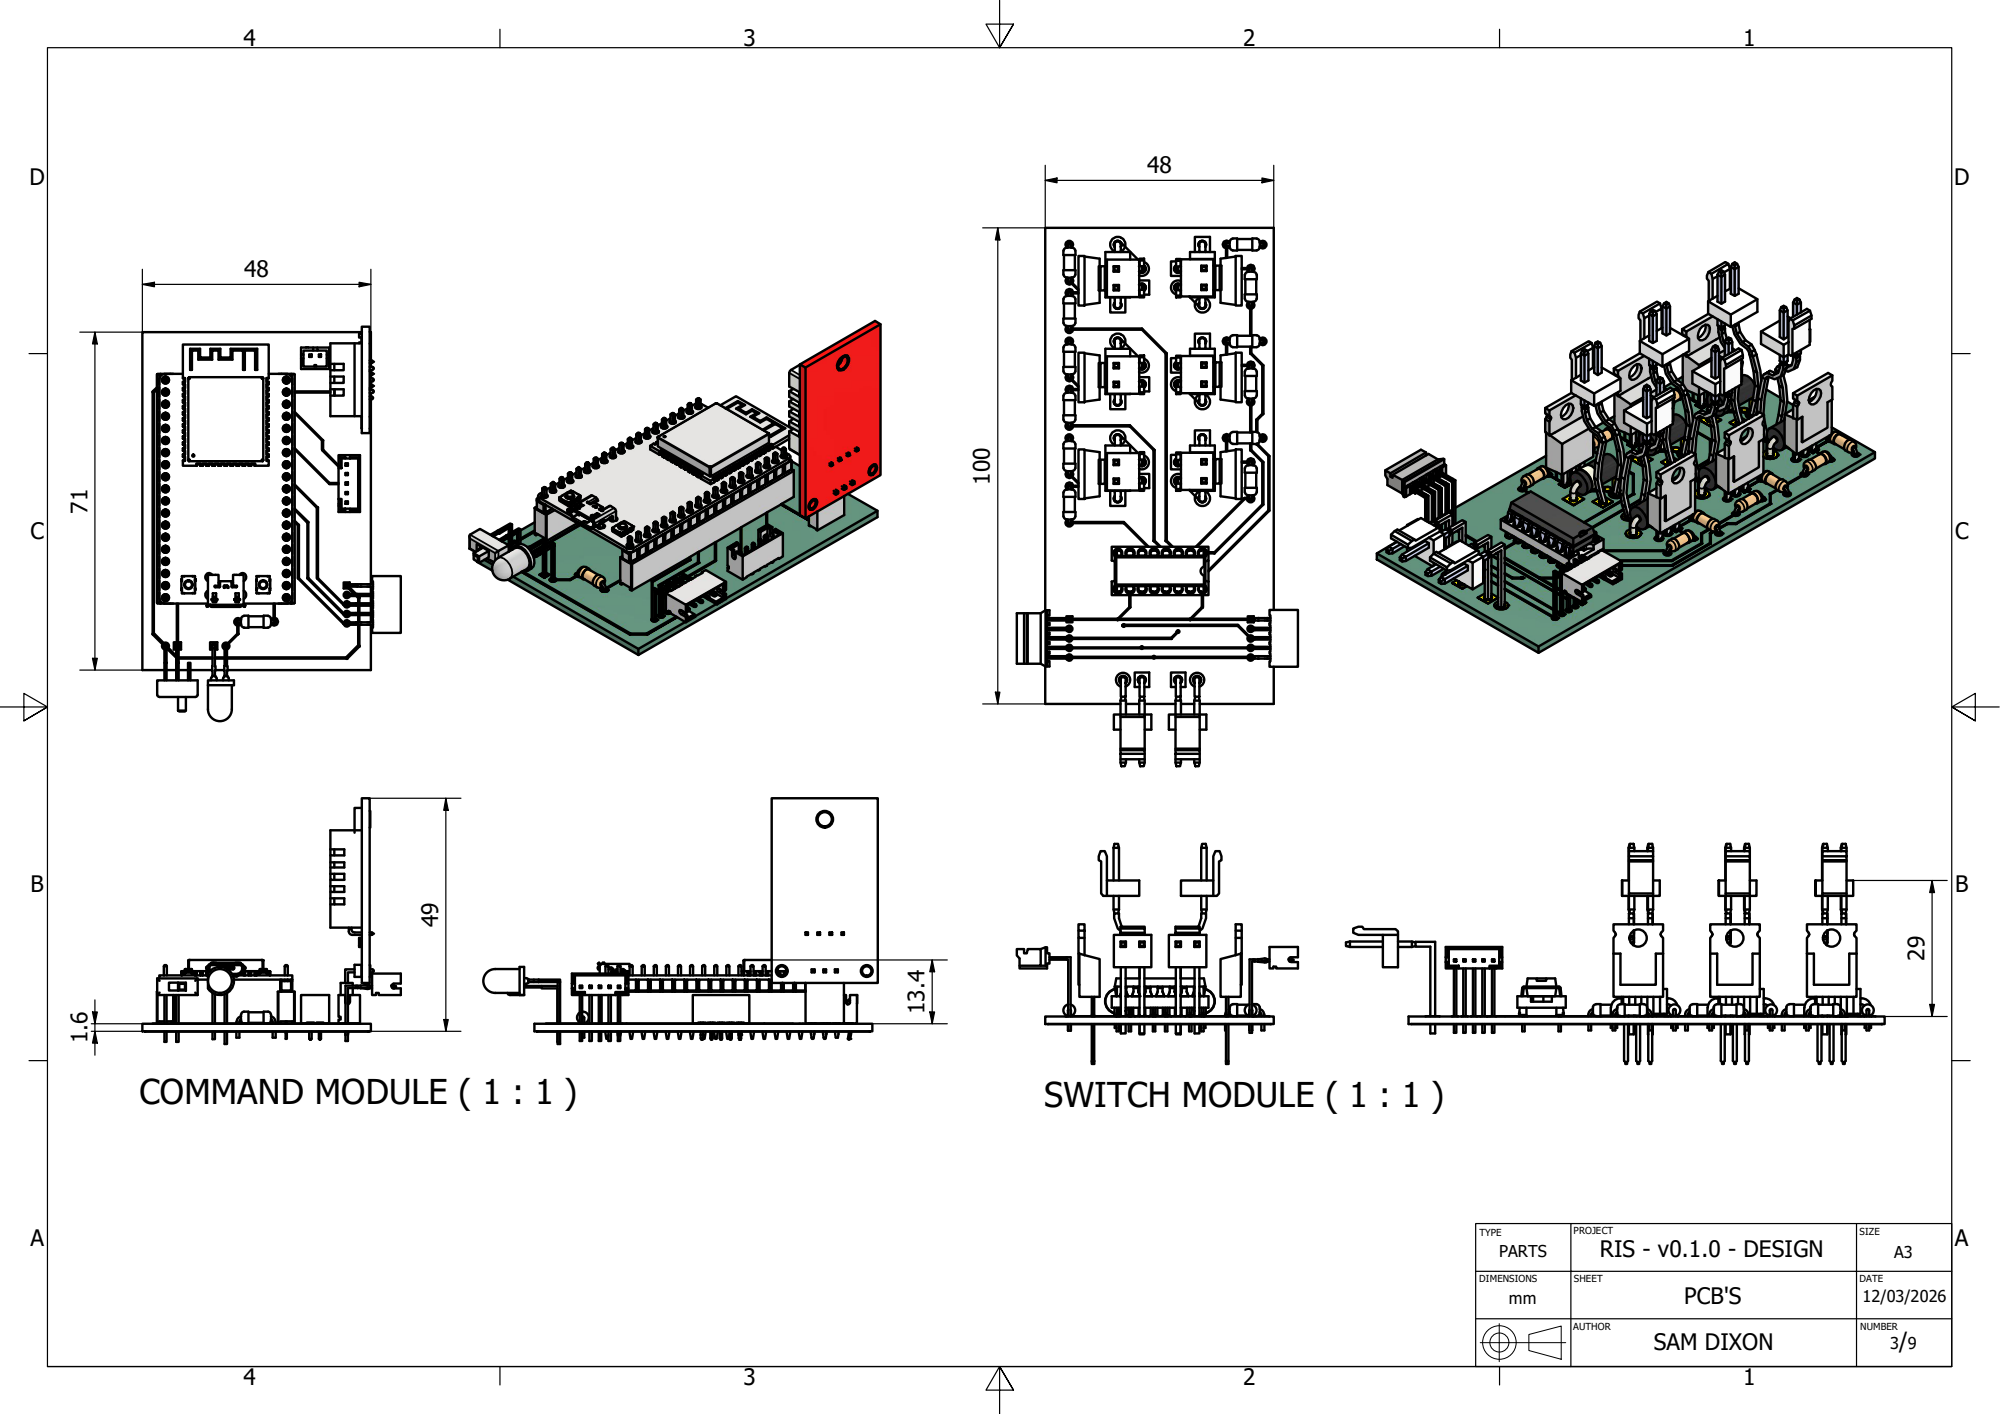
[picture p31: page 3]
COMMAND MODULE ( 1 : 1 ); SWITCH MODULE ( 1 : 1 ); RIS - v0.1.0 - DESIGN

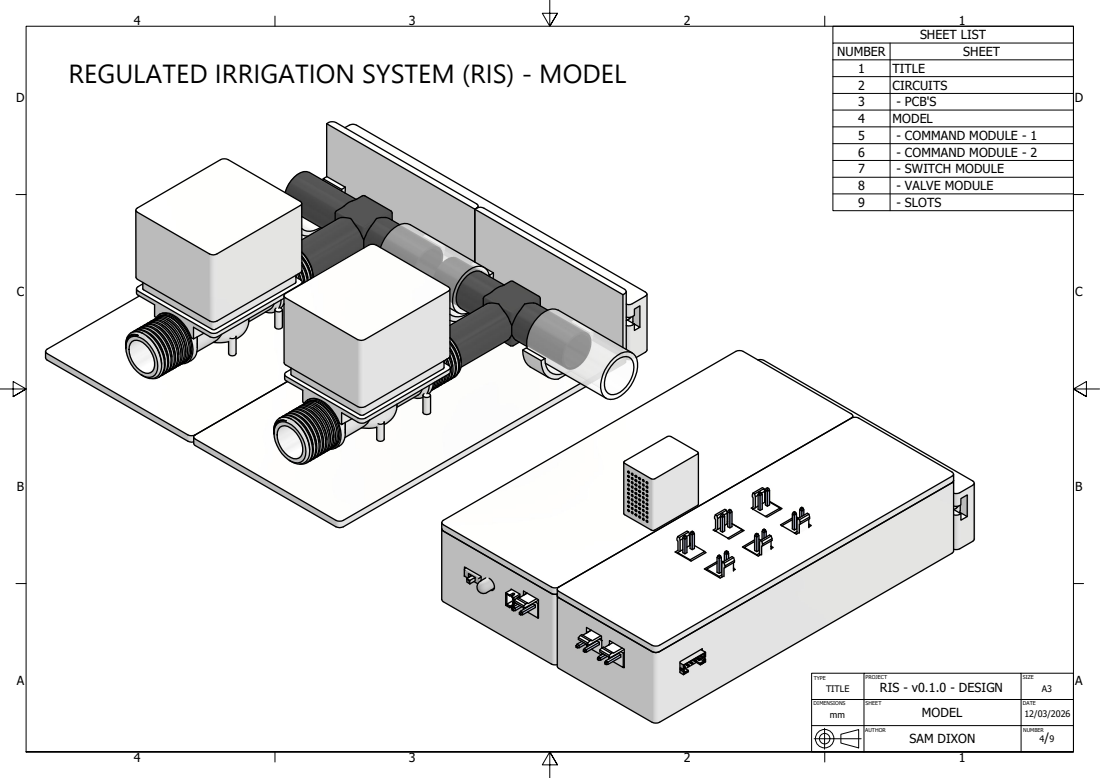
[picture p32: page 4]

SHEET LIST

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

REGULATED IRRIGATION SYSTEM (RIS) - MODEL

TYPE TITLE | PROJECT RIS - v0.1.0 - DESIGN | SIZE A3

DIMENSIONS | SHEET MODEL | DATE

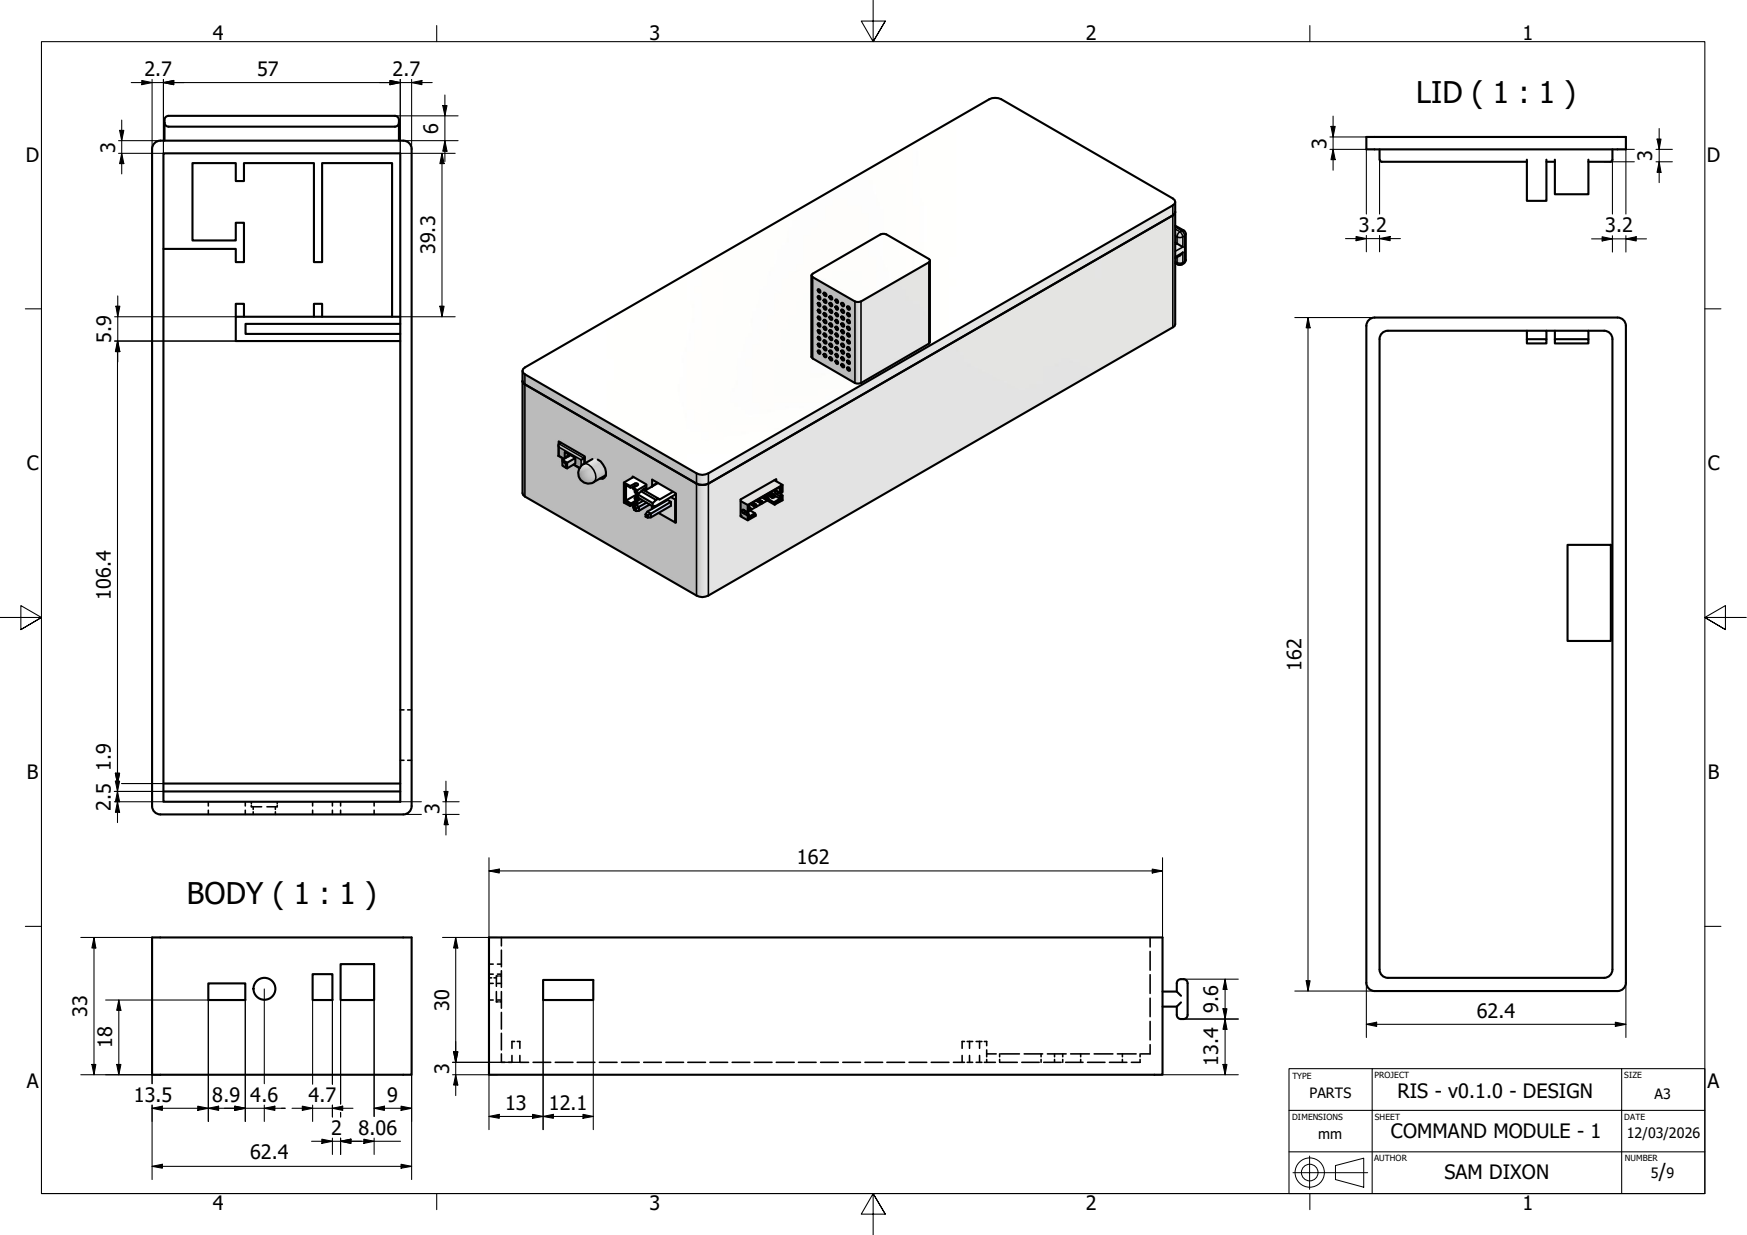
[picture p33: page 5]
BODY ( 1 : 1 ); LID ( 1 : 1 )

TYPE PARTS | PROJECT RIS - v0.1.0 - DESIGN | SIZE A3

DIMENSIONS | SHEET COMMAND MODULE - 1 | DATE

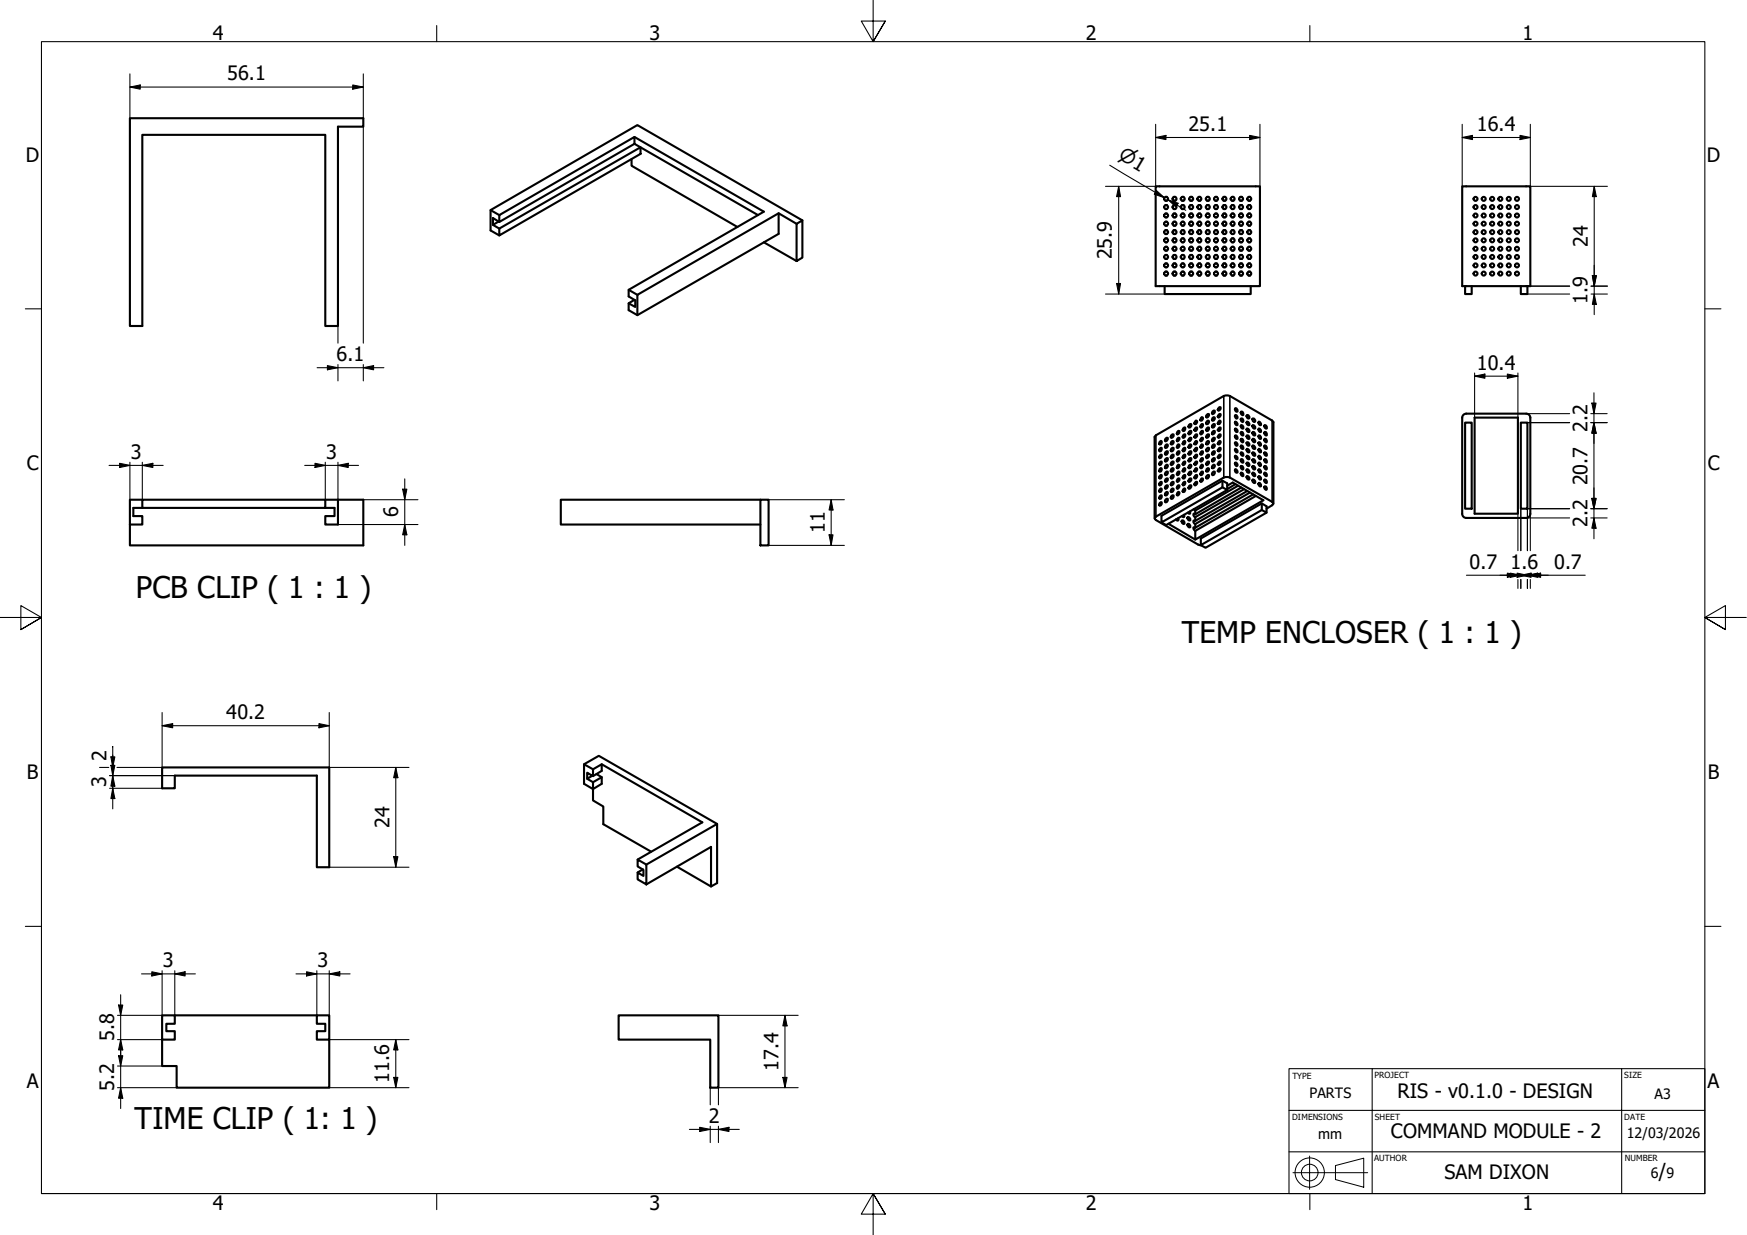
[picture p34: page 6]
PCB CLIP ( 1 : 1 ); TIME CLIP ( 1: 1 ); TEMP ENCLOSER ( 1 : 1 )

TYPE PARTS | PROJECT RIS - v0.1.0 - DESIGN | SIZE A3

DIMENSIONS | SHEET COMMAND MODULE - 2 | DATE

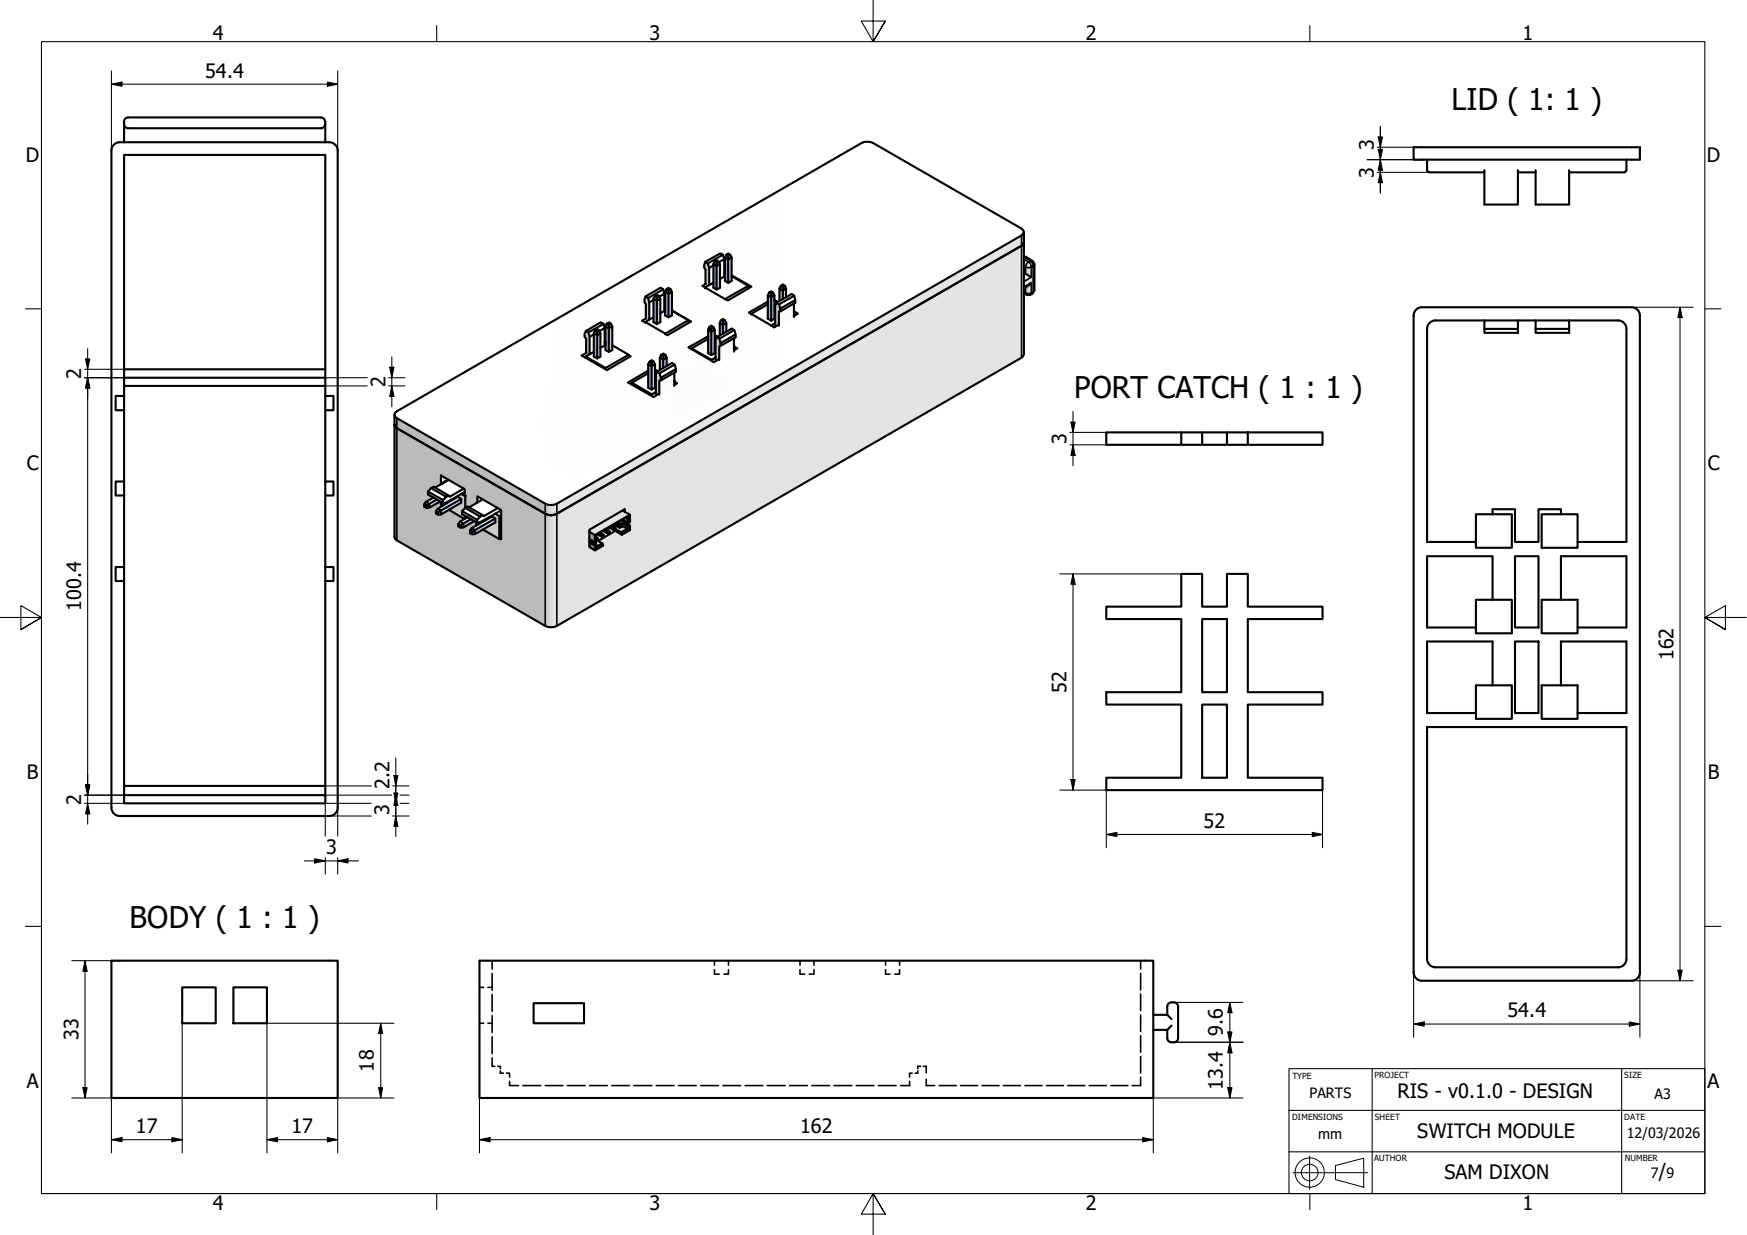
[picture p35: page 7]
BODY ( 1 : 1 ); LID ( 1: 1 ); PORT CATCH ( 1 : 1 )

TYPE PARTS | PROJECT RIS - v0.1.0 - DESIGN | SIZE A3

DIMENSIONS | SHEET SWITCH MODULE | DATE

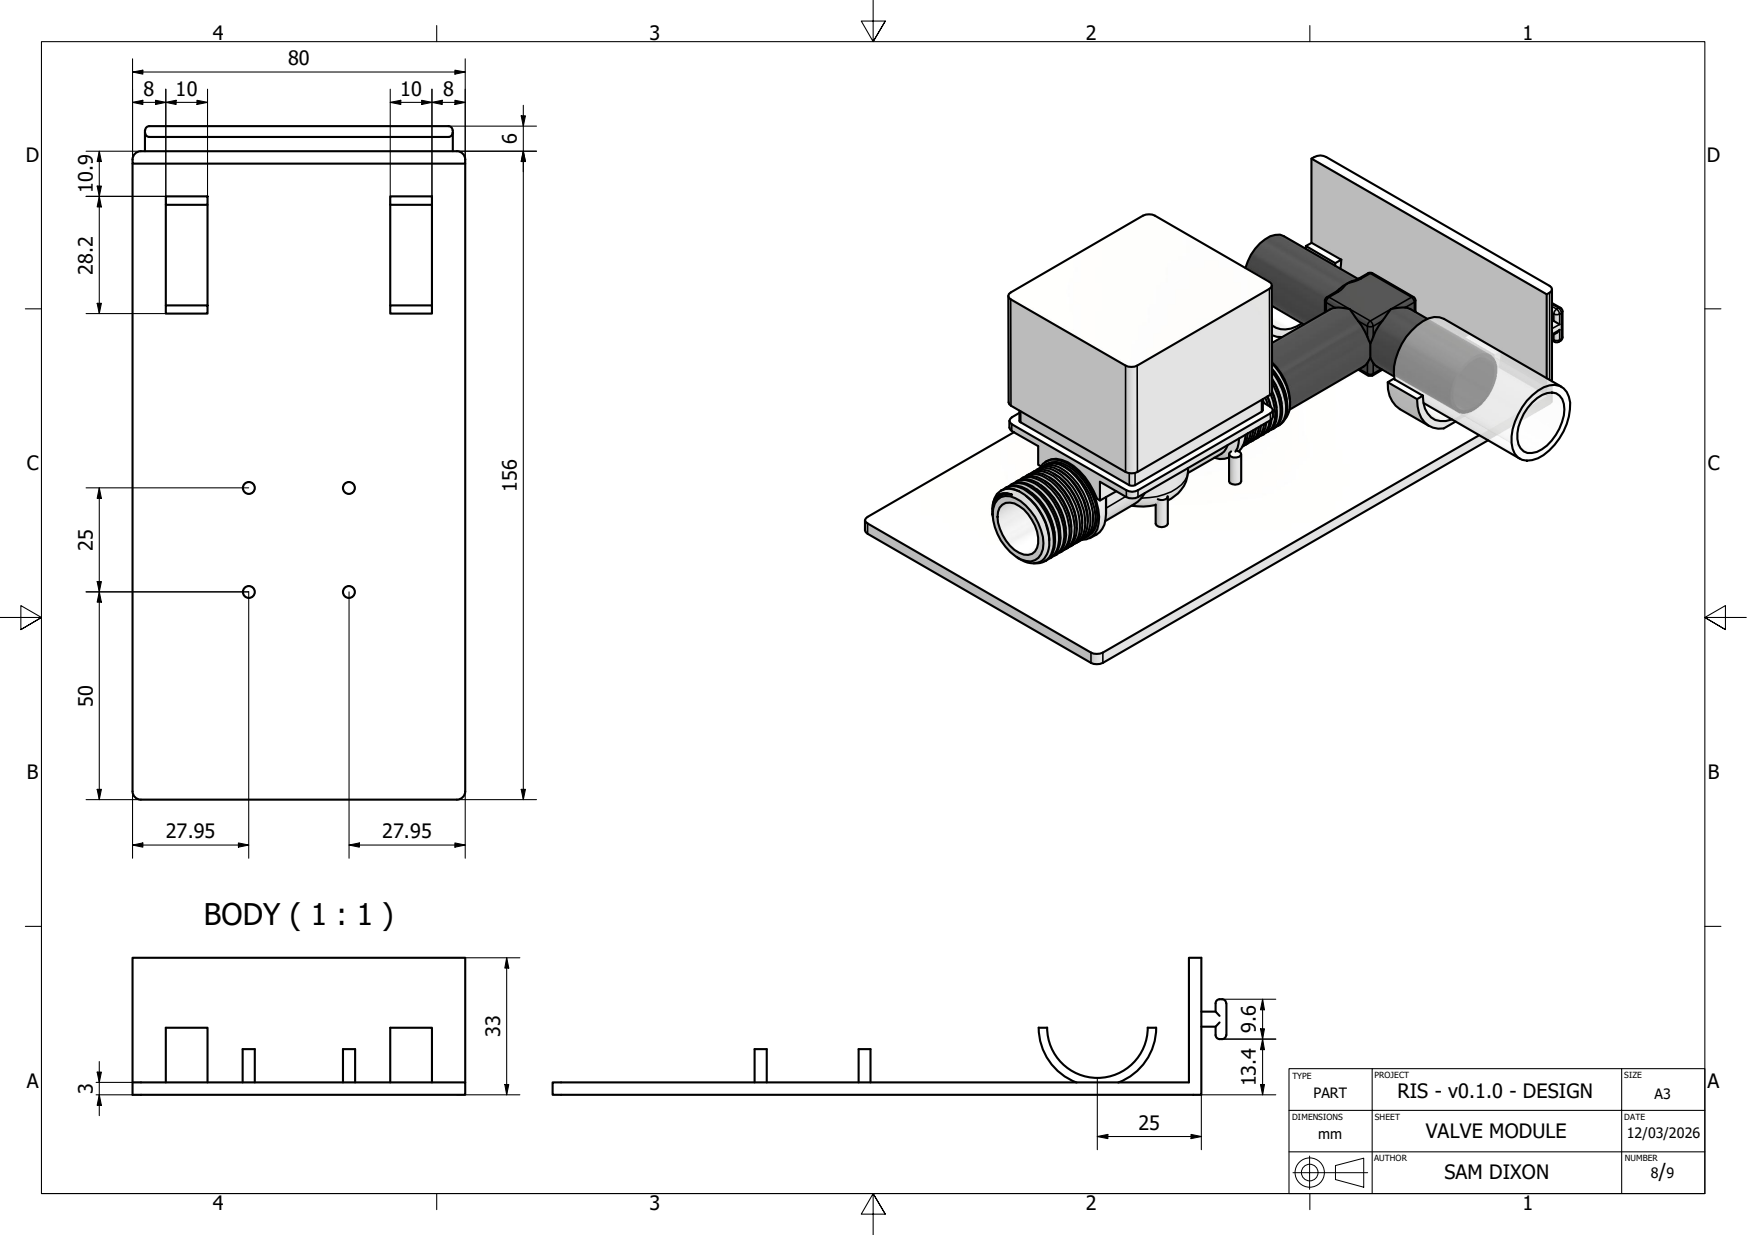
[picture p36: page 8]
BODY ( 1 : 1 )

TYPE PART | PROJECT RIS - v0.1.0 - DESIGN | SIZE A3

DIMENSIONS | SHEET VALVE MODULE | DATE

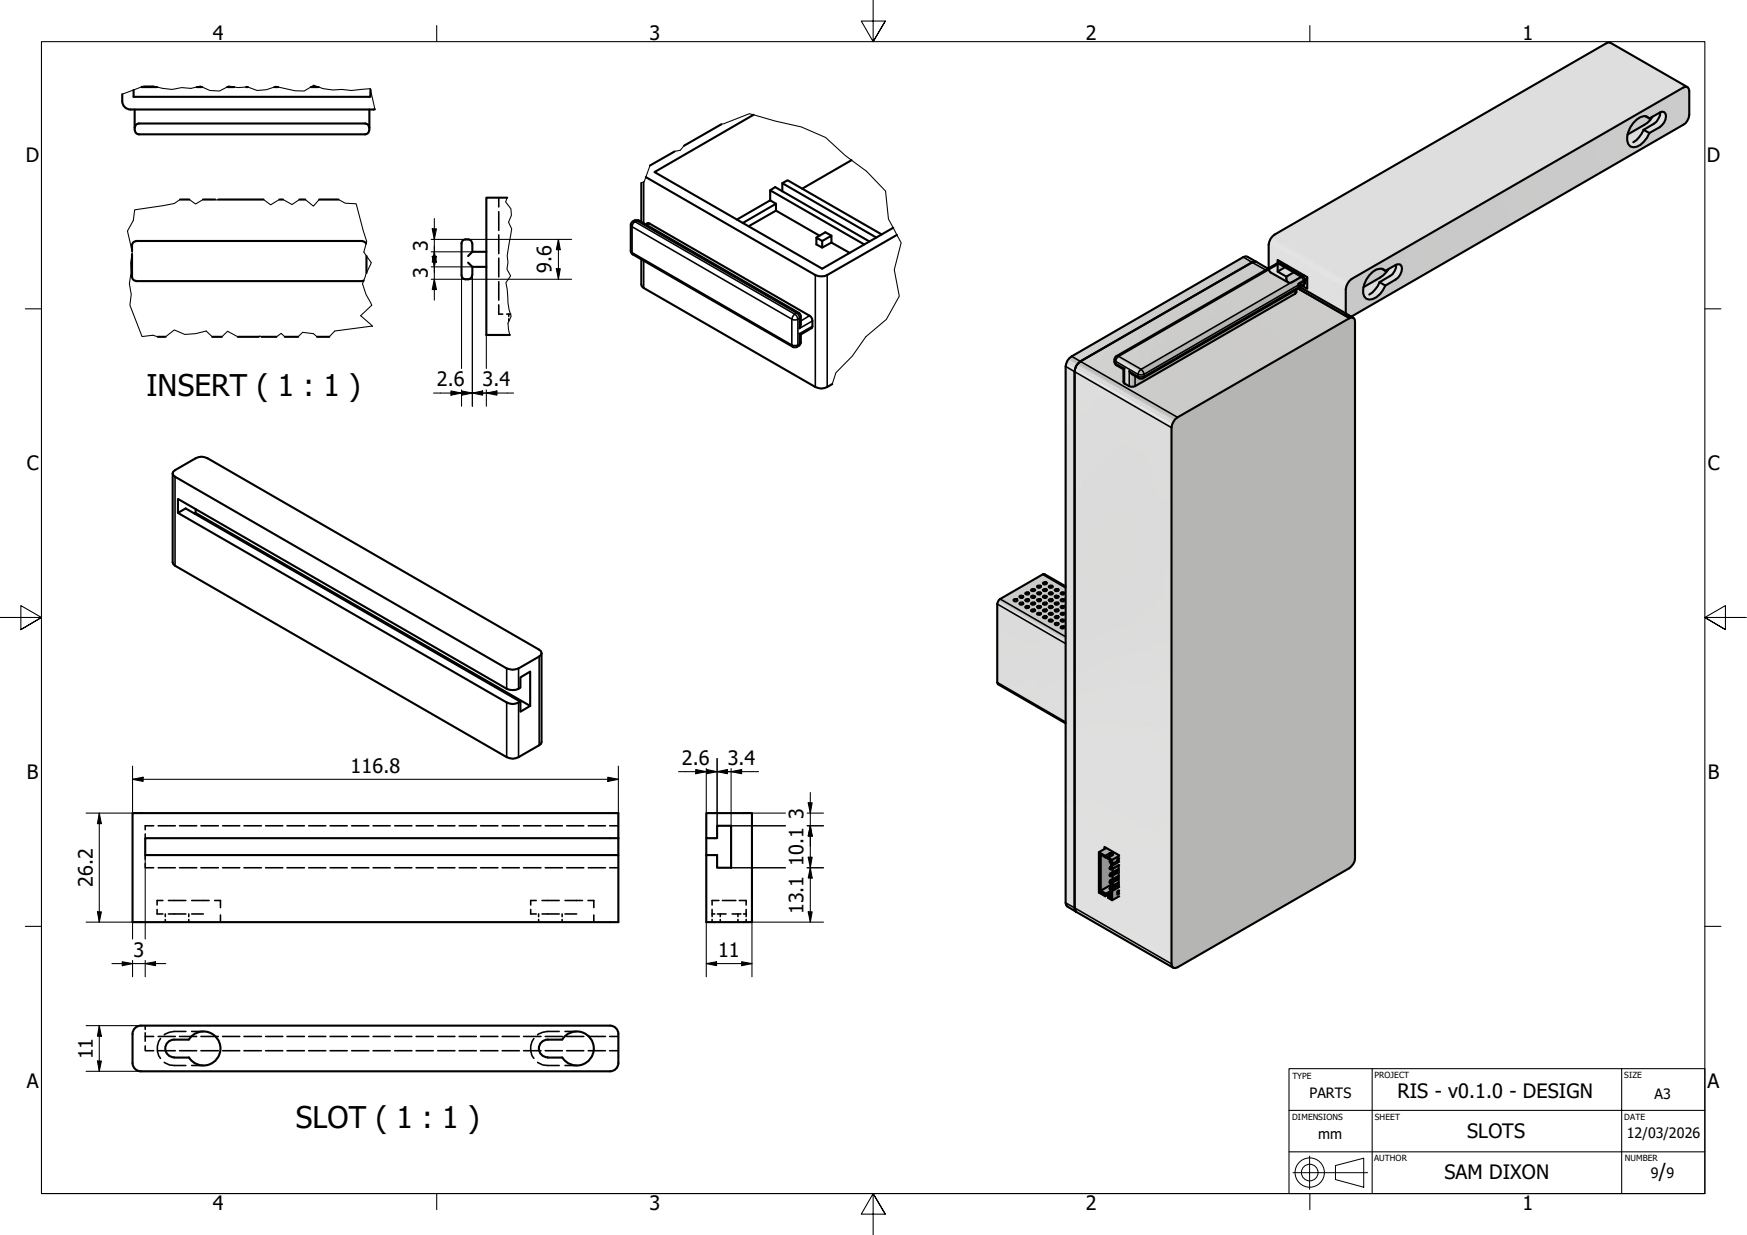
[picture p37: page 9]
SLOT ( 1 : 1 ); INSERT ( 1 : 1 )

TYPE PARTS | PROJECT RIS - v0.1.0 - DESIGN | SIZE A3

DIMENSIONS | SHEET SLOTS | DATE

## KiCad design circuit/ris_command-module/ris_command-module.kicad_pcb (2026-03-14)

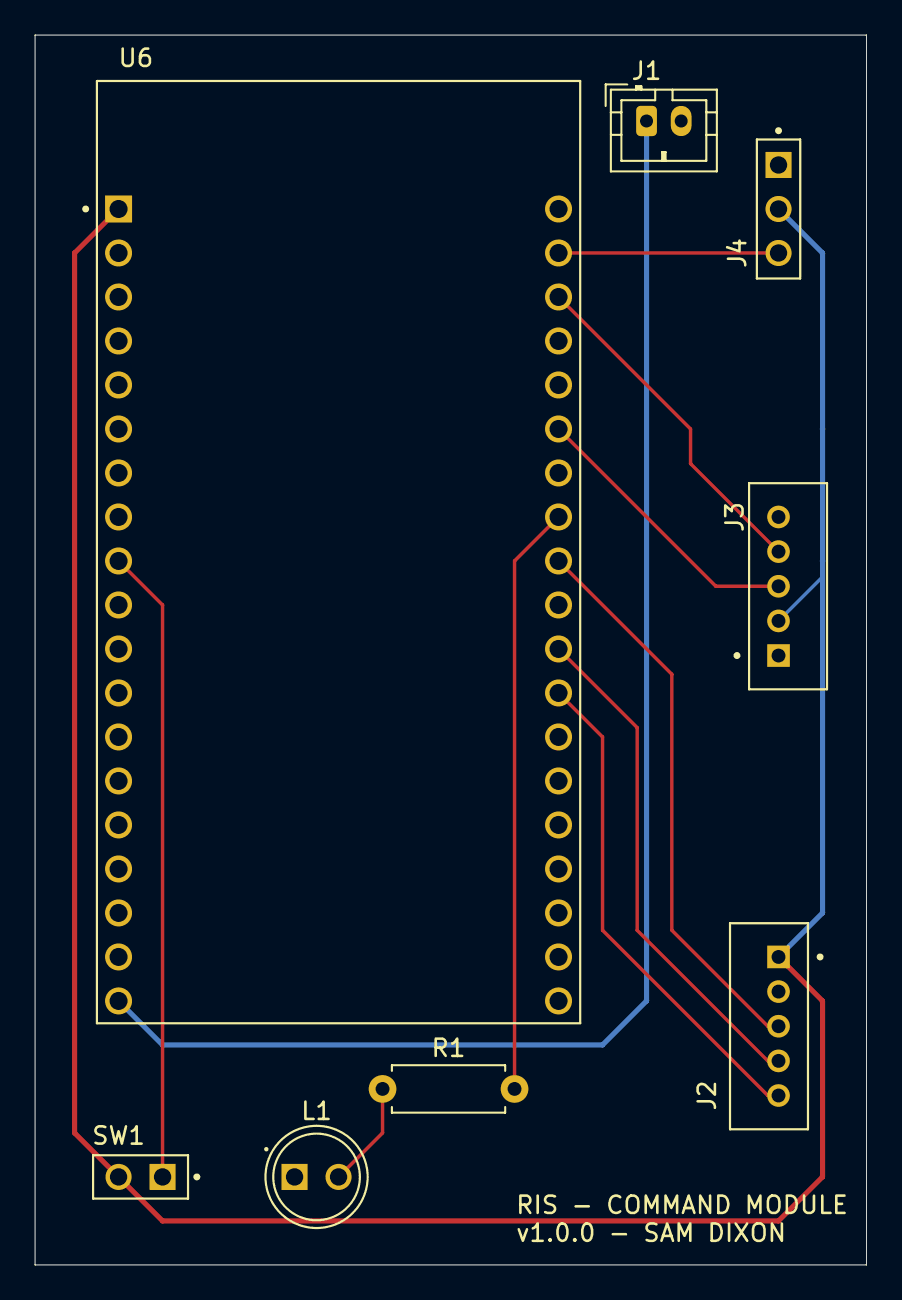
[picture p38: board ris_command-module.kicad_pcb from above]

Board: 2 copper layers, 48.0 x 71.0 mm, 8 parts (0 on the bottom side), 12 nets.

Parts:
J1: JST-PH-2P-M_5V; JST_PH_B2B-PH-K_1x02_P2.00mm_Vertical
J2: JST-PH-5P-M; JST_B5B-PH-K-S
J3: JST-PH-5P-M_ZS042; JST_B5B-PH-K-S
J4: Header-3P-F_DHT22; HARWIN_M20-7820346
L1: WP7113ID; LED_WP7113ID
R1: R-220; R_Axial_DIN0207_L6.3mm_D2.5mm_P7.62mm_Horizontal
SW1: SW_DIP_x01; HARWIN_M20-7820242
U6: ESP32-DEVKITC-32D; MODULE_ESP32-DEVKITC-32D

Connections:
+3.3V: J2.1, J3.2, J4.2, SW1.2, U6.J2-1 (3V3)
+5V: J1.1, U6.J2-19 (EXT_5V)
GND: J1.2, J2.2, J3.1, J4.1, L1.C, U6.J3-1 (GND3)
unnamed: J2.3, U6.J3-9 (IO18)
unnamed: J2.4, U6.J3-11 (IO17)
unnamed: J2.5, U6.J3-12 (IO16)
unnamed: J3.3, U6.J3-6 (IO21)
unnamed: J3.4, U6.J3-3 (IO22)
unnamed: J4.3, U6.J3-2 (IO23)
unnamed: L1.A, R1.1
unnamed: R1.2, U6.J3-8 (IO19)
unnamed: SW1.1, U6.J2-9 (IO25)

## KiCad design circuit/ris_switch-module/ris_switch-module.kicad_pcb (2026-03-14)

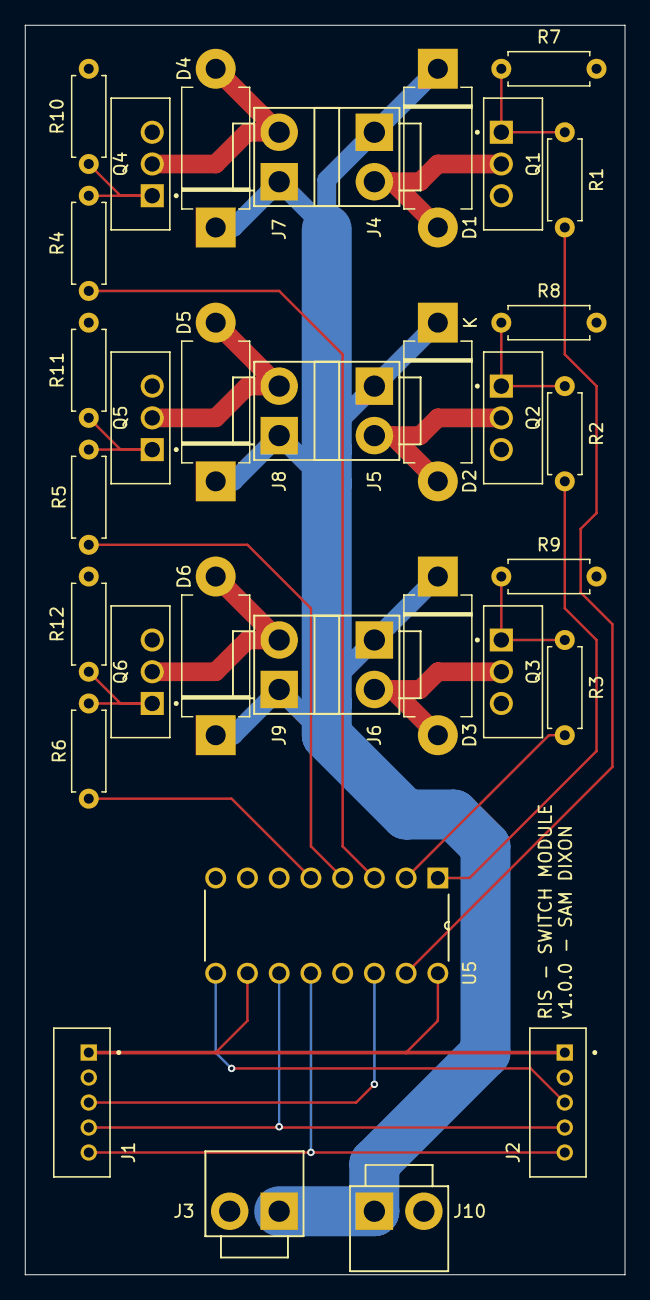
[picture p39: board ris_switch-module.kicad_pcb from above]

Board: 2 copper layers, 48.0 x 100.0 mm, 35 parts (0 on the bottom side), 25 nets.

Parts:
D1, D2, D3, D4, D5, D6: D; D_DO-201AD_P12.70mm_Horizontal
J1, J2: JST-PH-5P-M; JST_B5B-PH-K-S
J3, J10: JST-B2PS-VH-M; B2P-VH
J4, J5, J6, J7, J8, J9: JST-PH-2P-M; B2P-VH
Q1, Q2, Q3, Q4, Q5, Q6: IRLZ44N; TO254P1054X469X1930-3
R1, R2, R3, R4, R5, R6: R-220; R_Axial_DIN0207_L6.3mm_D2.5mm_P7.62mm_Horizontal
R7, R8, R9, R10, R11, R12: R-10k; R_Axial_DIN0207_L6.3mm_D2.5mm_P7.62mm_Horizontal
U5: 74HC595N_112; DIP254P762X420-16

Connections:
GND: J1.2, J2.2, J3.2, J10.2, Q1.3, Q2.3, Q3.3, Q4.3, Q5.3, Q6.3, R7.1, R8.1, R9.1, R10.1, R11.1, R12.1, U5.8 (GND), U5.13 (~OE)
unnamed: D1.2 (A), J4.2, Q1.2
unnamed: D1.1 (K), D2.1 (K), D3.1 (K), D4.1 (K), D5.1 (K), D6.1 (K), J3.1, J4.1, J5.1, J6.1, J7.1, J8.1, J9.1, J10.1
unnamed: D2.2 (A), J5.2, Q2.2
unnamed: D3.2 (A), J6.2, Q3.2
unnamed: D4.2 (A), J7.2, Q4.2
unnamed: D5.2 (A), J8.2, Q5.2
unnamed: D6.2 (A), J9.2, Q6.2
unnamed: J1.1, J2.1, U5.10 (~MR), U5.16 (VCC)
unnamed: J1.3, U5.14 (DS)
unnamed: J1.4, J2.4, U5.11 (SH_CP)
unnamed: J1.5, J2.5, U5.12 (ST_CP)
unnamed: J2.3, U5.9 (Q7_2)
unnamed: Q1.1, R1.2, R7.2
unnamed: Q2.1, R2.2, R8.2
unnamed: Q3.1, R3.2, R9.2
unnamed: Q4.1, R4.2, R10.2
unnamed: Q5.1, R5.2, R11.2
unnamed: Q6.1, R6.2, R12.2
unnamed: R1.1, U5.15 (Q0)
unnamed: R2.1, U5.1 (Q1)
unnamed: R3.1, U5.2 (Q2)
unnamed: R4.1, U5.3 (Q3)
unnamed: R5.1, U5.4 (Q4)
unnamed: R6.1, U5.5 (Q5)

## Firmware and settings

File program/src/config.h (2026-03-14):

#pragma once

//#define DEBUG

#define SERIAL_BAUD_RATE 115200
#define SWITCH_BIT_WIDTH 6

// Wi-Fi
#define DEFAULT_SSID "ris"
#define DEFAULT_PASSWORD "admin123"

// Pins
#define LED_PIN 19              // Out
#define TEMP_SENSOR_PIN 23      // In/Out
#define WIFI_SWITCH_PIN 25      // In

// GPIO 21  (I²C SDA)
// GPIO 22  (I²C SCL)

// Outputs to 74HC595 Chip
#define SWITCH_DATA_PIN 18      // Out
#define SWITCH_SRCLK_PIN 17     // Out: Write Internal Clock
#define SWITCH_RCLK_PIN 16      // Out: Output Clock

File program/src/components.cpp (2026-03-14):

#include "components.h"

#include <stdint.h>

#include <Arduino.h>
#include <DHT.h>
#include <RTClib.h>
#include <Wire.h>
#include <esp_sleep.h>

#include "core.h"

DHT dht(TEMP_SENSOR_PIN, DHT22);

RTC_DS3231 rtcExternal;
RTC_Millis rtcInternal;
bool externalRTC = true;

std::vector<uint8_t> portStates;
std::vector<uint8_t> currentPortStates;

void SetupComponents() {
    pinMode(LED_PIN, OUTPUT);
    pinMode(WIFI_SWITCH_PIN, INPUT_PULLDOWN);
    
    pinMode(SWITCH_DATA_PIN, OUTPUT);
    pinMode(SWITCH_SRCLK_PIN, OUTPUT);
    pinMode(SWITCH_RCLK_PIN, OUTPUT);
    
    dht.begin();
    Wire.begin();

    portStates = {};
    currentPortStates = {};

    if (!rtcExternal.begin()) {
        LOGf("External RTC Not Found - Using Internal RTC\n");

        rtcInternal.begin(DateTime(2000, 1, 1, 0, 0, 0));

        externalRTC = false;
    }

	LOGf("Components Setup\n");
}

void LightSleep(uint32_t seconds) {
    if (seconds == 0) {
        return;
    }

    LOGf("Light Sleep: %d\n", seconds);
    
    pinMode(WIFI_SWITCH_PIN, INPUT);

    esp_sleep_enable_timer_wakeup((uint64_t)seconds * 1000000ULL);
    esp_sleep_enable_ext0_wakeup((gpio_num_t)WIFI_SWITCH_PIN, 1);
    esp_light_sleep_start();

    pinMode(WIFI_SWITCH_PIN, INPUT_PULLDOWN);
    
    LOGf("Exit Light Sleep\n");
}

int GetTemp() {
    int temp = (int)dht.readTemperature();
    
    if (temp < -40 || temp > 80) {
        temp = 0;
    }
    LOGf("Temp: %d\n", temp);

    return temp;
}
bool GetWifiSwitchStatus() {
    return digitalRead(WIFI_SWITCH_PIN);
    //return true;
}
void SetLED(bool state) {
    digitalWrite(LED_PIN, state);

    LOGf("LED State: %d\n", state);
}

Time GetTime() {
    DateTime now;
    if (externalRTC) {
        now = rtcExternal.now();
    }
    else {
        now = rtcInternal.now();
    }

    Time time = {};
    time.sec = now.second();
    time.min = now.minute();
    time.hour = now.hour();
    time.dayDate = now.day();
    time.month = now.month();
    time.year = now.year();

    return time;
}
void SetTime(const Time& time) {
    DateTime newTime(time.year, time.month, time.dayDate, time.hour, time.min, time.sec);
    
    if (externalRTC) {
        rtcExternal.adjust(newTime);
    }
    else {
        rtcInternal.adjust(newTime);
    }
}

uint32_t GetTimeSeconds() {
    DateTime now;
    if (externalRTC) {
        now = rtcExternal.now();
    }
    else {
        now = rtcInternal.now();
    }
    uint32_t timeSeconds = now.unixtime();
    
    return timeSeconds;
}
void SetTimeSeconds(uint32_t seconds) {
    if (externalRTC) {
        rtcExternal.adjust(DateTime(seconds));
    }
    else {
        rtcInternal.adjust(DateTime(seconds));
    }
}

uint32_t ConvertTimeToSeconds(const Time& time) {
    DateTime newTime(time.year, time.month, time.dayDate, time.hour, time.min, time.sec);

    return newTime.unixtime();
}

void EnableSwitchPorts(std::vector<uint32_t> ports) {
    for (int i = 0; i < ports.size(); i++) {
        while (portStates.size() <= ports[i]) {
            portStates.push_back(0);
        }
        LOGf("Enable Port: %d\n", ports[i]);
        portStates[ports[i]] = 1;
        LOGf("... Port: %d\n", portStates[ports[i]]);
    }
}
void DisableSwitchPorts(std::vector<uint32_t> ports) {
    for (int i = 0; i < ports.size(); i++) {
        while (portStates.size() <= ports[i]) {
            portStates.push_back(0);
        }
        LOGf("Disable Port: %d\n", ports[i]);
        portStates[ports[i]] = 0;
    }
}

void UpdateSwitchPorts(int bitWidth) {
    if (currentPortStates == portStates || portStates.size() == 0 || bitWidth <= 0 || bitWidth > 8) { // Check Changed
        return;
    }

    digitalWrite(SWITCH_DATA_PIN, LOW);
    digitalWrite(SWITCH_SRCLK_PIN, LOW);
	digitalWrite(SWITCH_RCLK_PIN, LOW);
    
    // Write Internally to 74HC595 Shift Register
    int remainingPorts = portStates.size();
    int portIndex = portStates.size() - 1;

    while (remainingPorts > 0) {
        int registerDataBits = (remainingPorts >= bitWidth) ? bitWidth : remainingPorts;
        
        LOGf("Padding: ");
        
        // Padding
        if (registerDataBits == bitWidth) {
            for (int i = 0; i < (8 - bitWidth); i++) {
                digitalWrite(SWITCH_DATA_PIN, LOW);
                
                digitalWrite(SWITCH_SRCLK_PIN, HIGH);
                digitalWrite(SWITCH_SRCLK_PIN, LOW);
                
                LOGf("0, ");
            }
        }
        LOGf("\n");

        LOGf("Update Port Row: ");
        
        // Shift Data Bits
        for (int i = 0; i < registerDataBits; i++) {
            digitalWrite(SWITCH_DATA_PIN, portStates[portIndex]);

            digitalWrite(SWITCH_SRCLK_PIN, HIGH);
            digitalWrite(SWITCH_SRCLK_PIN, LOW);

            LOGf("%d-%d ", portStates[portIndex], portIndex);

            portIndex--;
        }
        LOGf("\n");

        remainingPorts -= registerDataBits;
    }
    
    // Output 74HC595 Shift Register Internals
    digitalWrite(SWITCH_RCLK_PIN, HIGH);
    digitalWrite(SWITCH_RCLK_PIN, LOW);

    digitalWrite(SWITCH_DATA_PIN, LOW);

    currentPortStates = portStates;
}
